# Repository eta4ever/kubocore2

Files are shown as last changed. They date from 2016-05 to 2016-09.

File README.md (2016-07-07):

3D-принтер Kubocore 2. Дальний родственник SmartCore. Точнее, был первый Kubocore, который форк SmartCore из алюминиевой трубы. А второй - из конструкционного профиля 2020 и на рельсах MGN12. Общего со SmartCore - кинематика CoreXY двухуровневая и подшипники 608zz в качестве роликов.

Все изображено в "Компас-3D". Актуальная сборка - assembly_v3 в корне. Parts - просто детали. Printed parts - соответственно, печатные.

В общем, кубик из 2020, уголки печатные, Т-гайки китайские, рельсы нетипично расположены, чтобы уменьшить подъем ремней - для двух уровней сильно актуально. Печатает. 

http://3dtoday.ru/tag/kubocore+2/

---

Чуток подробностей. Тезисно.

--XY--

8 подшипников 60zz в качестве роликов ремней. Насажены на обрезки валов 8 мм, проложены печатными шайбами.

П-образный профиль 12х15 мм под рельсой X. 

Ремни натягиваются ручками. Для компенсации неравномерности натяга можно дополнительно подтянуть ремни подручными средствами (ну, там, пружинкой от прищепки) на участке за печатающей головкой (там перехлест, "правый" ремень идет к левому краю и наоборот).

Хотэнд E3D (в моем случае Volcano) крепится за верхнее горлышко алюминиевым держателем 16-миллиметрового вала (SK16).

--Z--

Два вала 12 мм, соотв., 4 держателя SK12. Длинные фланцевые подшипники (LMF12LUU) прикручены к 12-миллиметровой фанере (насквозь), она - основание стола.

Ходовой винт - TR8x8 с латуниевой гайкой, муфта обычная "пружинка", в нее закинут шарик от подшипника, чтобы на наклон работала, а на сжатие - нет.

---

Держатели движков - от cnc-tehnologi.ru. Алярма, они не особо стандартные. Надо прикидывать, можно ли поставить обычные.

Остальное менее интересно. Электроника - любая подходящая. Работало оно на MKS Gen (Marlin 1.02), сейчас на MKS SBase (Smoothieware).

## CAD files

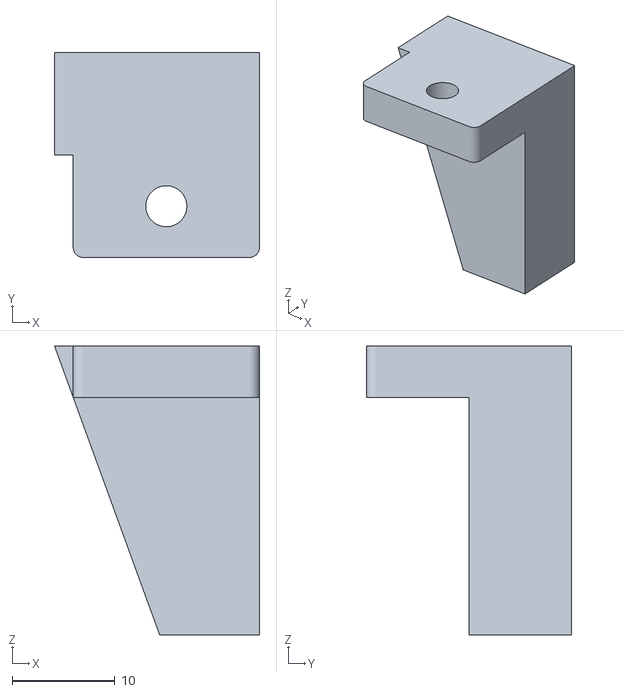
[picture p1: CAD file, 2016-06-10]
printed parts/fullgraphic-box-mountL.stl
20.0 x 20.0 x 28.2

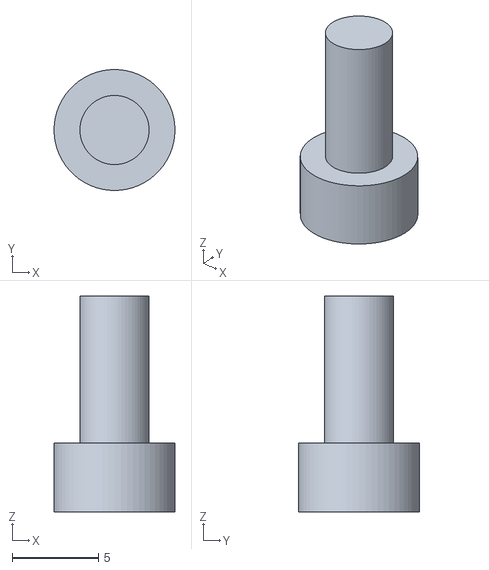
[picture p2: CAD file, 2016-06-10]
printed parts/fullgraphic-box-button.stl
7.00 x 7.00 x 12.5

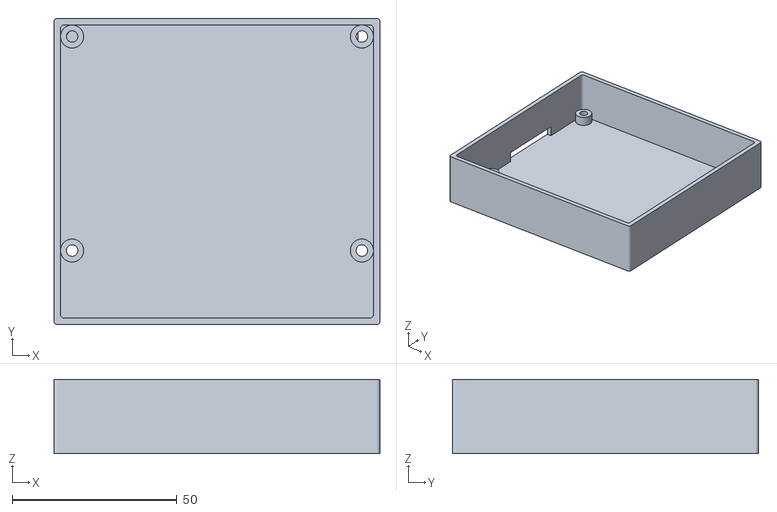
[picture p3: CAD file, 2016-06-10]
printed parts/fullgraphic-box.stl
99.0 x 93.0 x 22.5

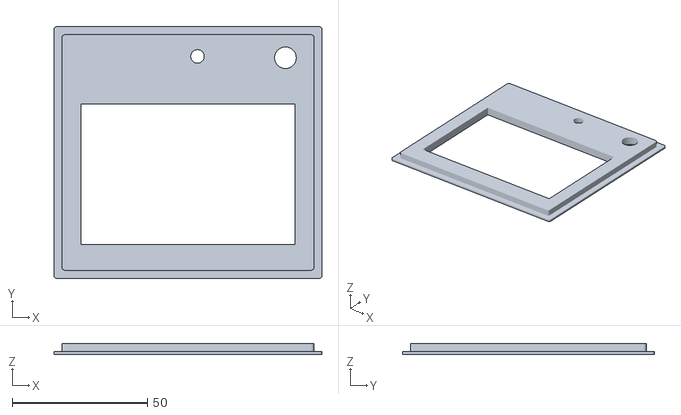
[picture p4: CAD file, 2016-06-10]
printed parts/fullgraphic-box-cover.stl
99.0 x 93.0 x 4.00

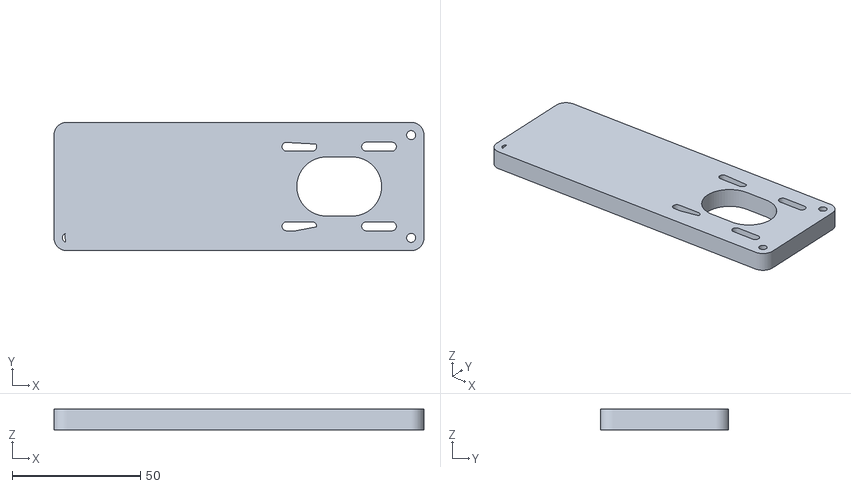
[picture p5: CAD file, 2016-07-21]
bandura extruder beta/printed/lid.stl
144.0 x 50.0 x 8.00

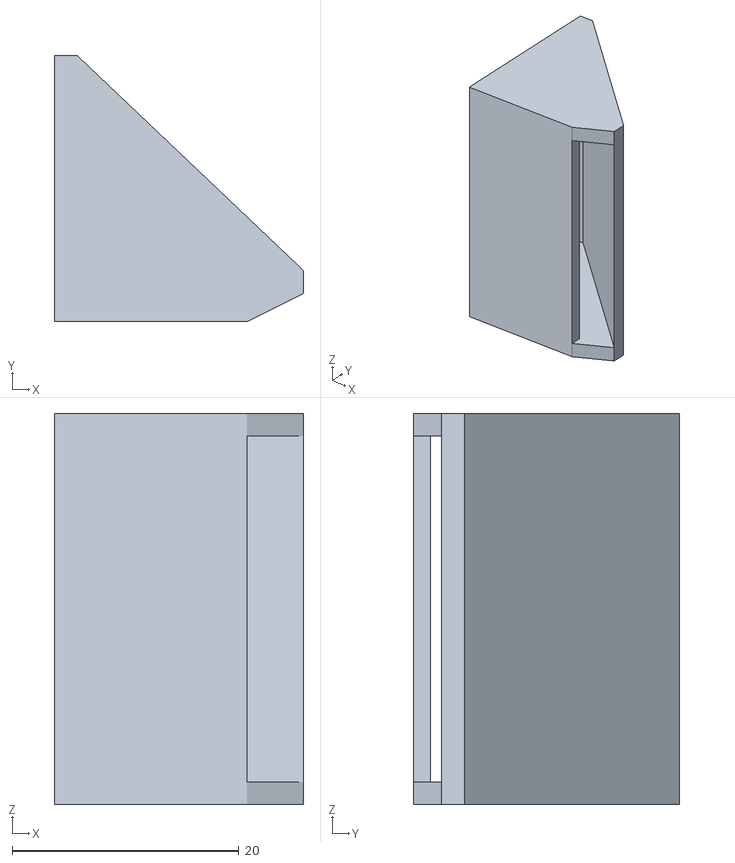
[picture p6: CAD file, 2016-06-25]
not used/printed parts/blower_nozzle_v2.stl
22.0 x 23.5 x 34.5

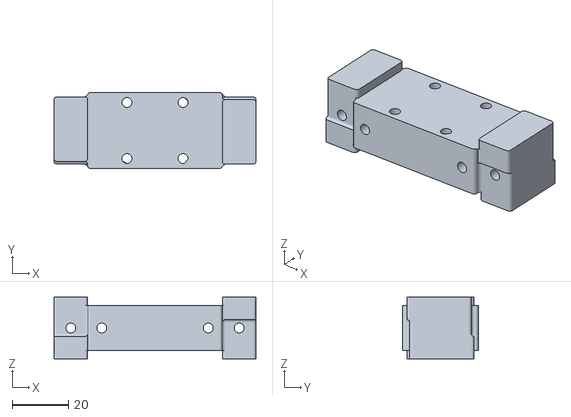
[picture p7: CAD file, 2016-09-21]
printed parts 2016-09-15/head_v3.stl
72.0 x 27.0 x 22.0

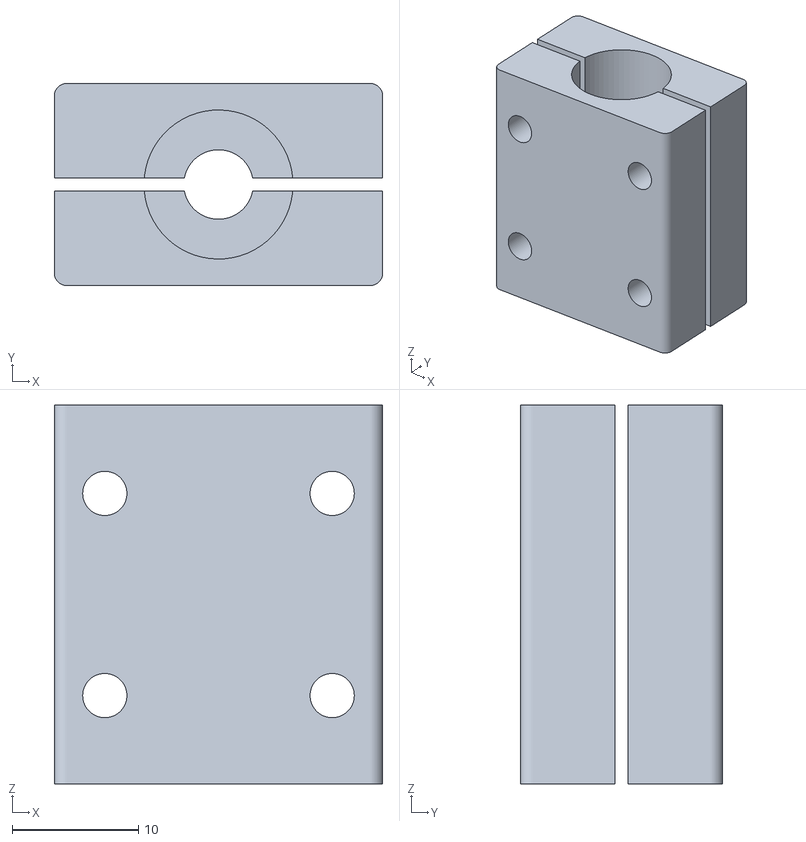
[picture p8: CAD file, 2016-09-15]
printed parts/5to11.5.stl
26.0 x 16.0 x 30.0

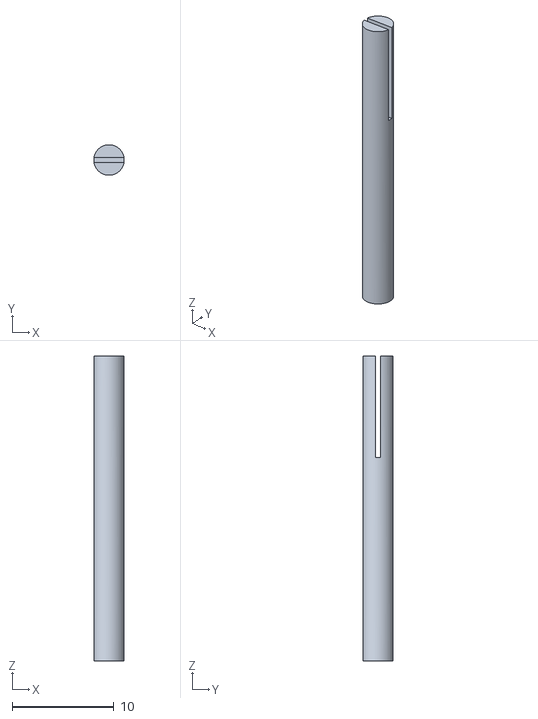
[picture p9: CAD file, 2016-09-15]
printed parts/e3dnewholder/pin.stl
3.00 x 3.00 x 30.0

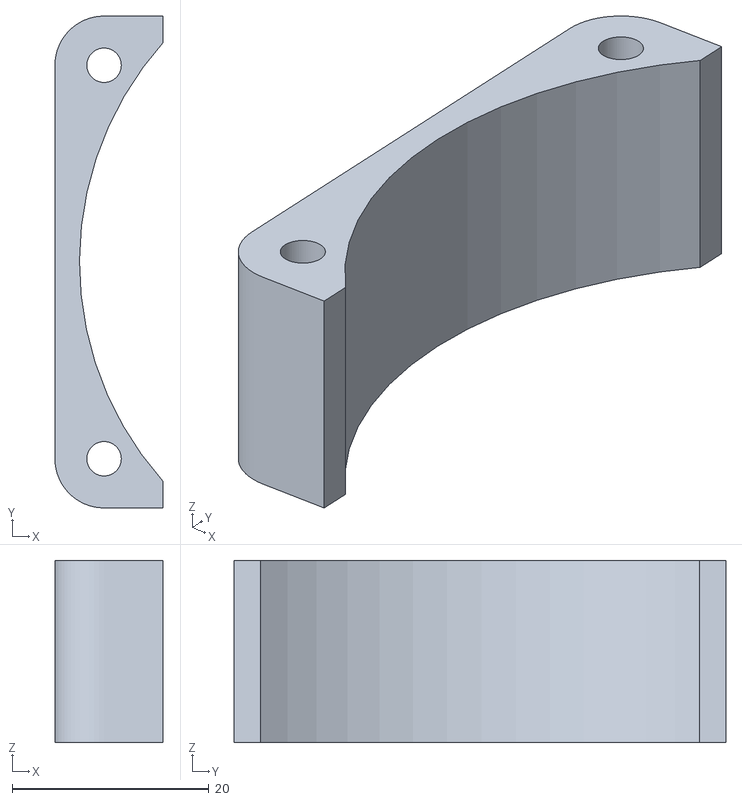
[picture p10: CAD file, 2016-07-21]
bandura extruder beta/printed/insert.stl
11.0 x 50.0 x 18.5

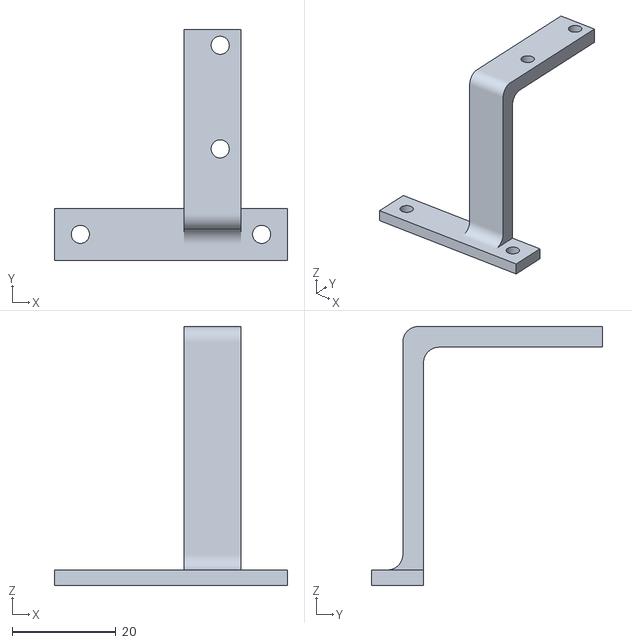
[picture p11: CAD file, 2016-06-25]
not used/printed parts/blower_holder_v3.stl
45.0 x 44.5 x 50.0

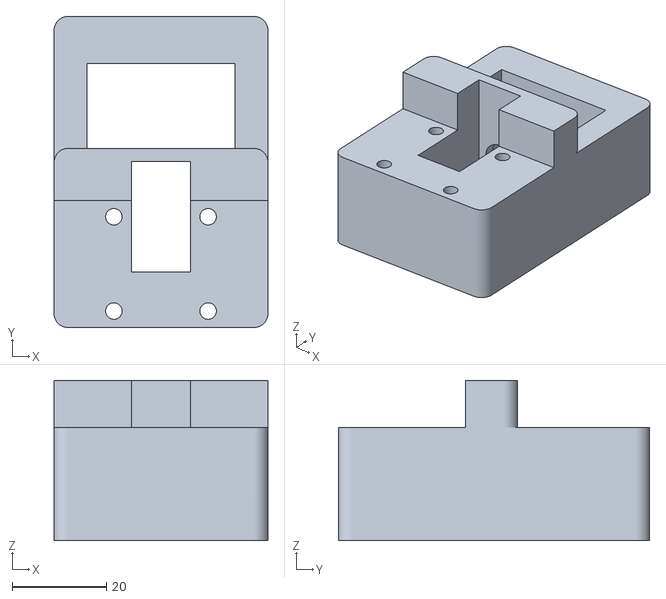
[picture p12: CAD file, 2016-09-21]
printed parts 2016-09-15/xy_v3_rep.stl
45.4 x 66.0 x 34.0

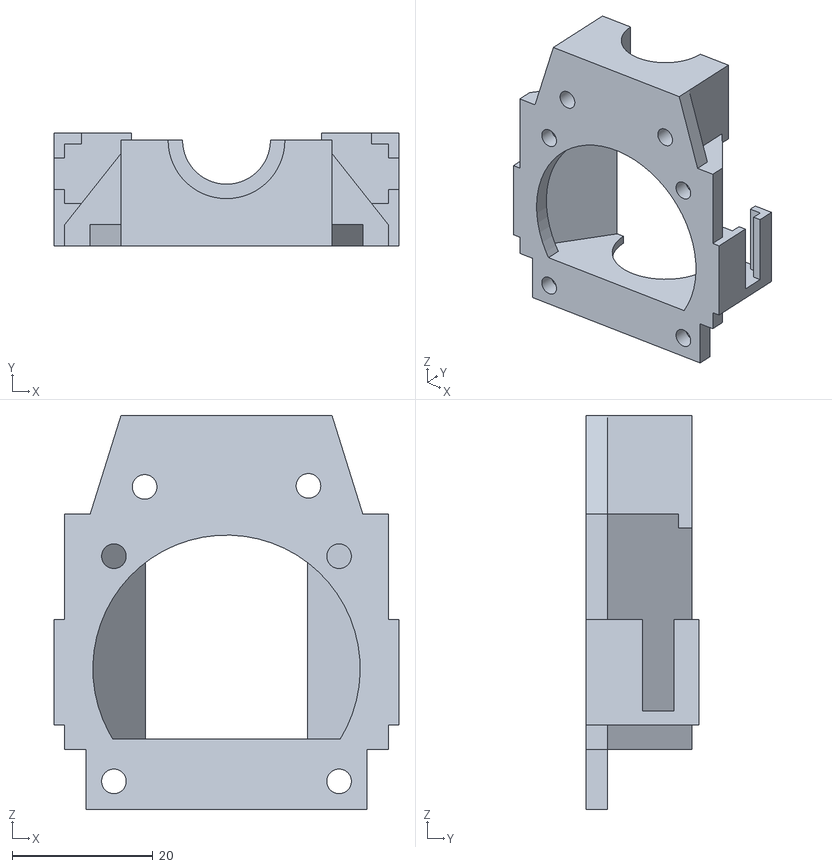
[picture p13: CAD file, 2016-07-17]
printed parts/e3dnewholder/front.stl
49.0 x 16.0 x 56.0

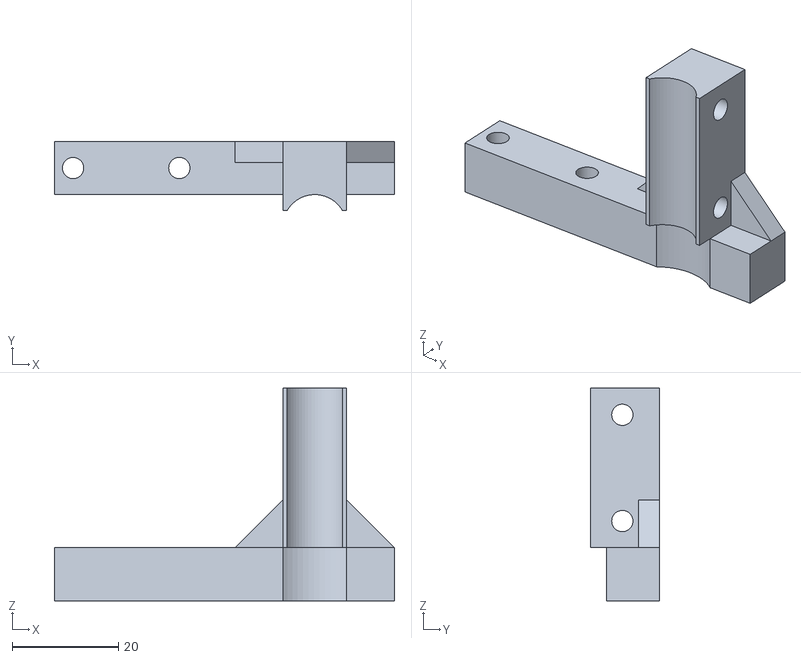
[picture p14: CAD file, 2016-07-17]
printed parts/hose_holder-head.stl
64.0 x 13.0 x 40.0

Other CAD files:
printed parts/fullgraphic-box-mountR.stl
not used/printed parts/blower_holder_v2_printable.stl
printed parts 2016-09-15/head_v3_rep.stl
printed parts/e3dnewholder/base.stl
not used/OpenSCAD parts - deprecated/head.scad
not used/OpenSCAD parts - deprecated/helper.scad
not used/OpenSCAD parts - deprecated/parts.scad
not used/OpenSCAD parts - deprecated/washer.scad
not used/OpenSCAD parts - deprecated/xy.scad
not used/OpenSCAD parts - deprecated/xyz.scad
not used/OpenSCAD parts - deprecated/z.scad
not used/printed parts/blower_holder_printable.stl
not used/printed parts/blower_nozzle.stl
not used/printed parts/z_console - 11.stl
not used/printed parts/z_console - 111.stl
not used/printed parts/z_console - 112.stl
not used/printed parts/z_console - 12.stl
not used/printed parts/z_console - 22.stl
not used/printed parts/z_console - 21.stl
not used/printed parts/z_console - 211.stl
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

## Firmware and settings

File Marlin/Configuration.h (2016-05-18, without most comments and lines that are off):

#define CONFIGURATION_H
#include "boards.h"
#define STRING_VERSION_CONFIG_H __DATE__ " " __TIME__ // build date and time
#define STRING_CONFIG_H_AUTHOR "(none, default config)" // Who made the changes.
#define SERIAL_PORT 0
#define BAUDRATE 115200
#define MOTHERBOARD 33
#define EXTRUDERS 1
#define POWER_SUPPLY 1
#define TEMP_SENSOR_0 1
#define TEMP_SENSOR_1 0
#define TEMP_SENSOR_2 0
#define TEMP_SENSOR_BED 1
#define MAX_REDUNDANT_TEMP_SENSOR_DIFF 10
#define TEMP_RESIDENCY_TIME 10  // (seconds)
#define TEMP_HYSTERESIS 3       // (degC) range of +/- temperatures considered "close" to the target one
#define TEMP_WINDOW     1       // (degC) Window around target to start the residency timer x degC early.
#define HEATER_0_MINTEMP 5
#define HEATER_1_MINTEMP 5
#define HEATER_2_MINTEMP 5
#define BED_MINTEMP 5
#define HEATER_0_MAXTEMP 275
#define HEATER_1_MAXTEMP 275
#define HEATER_2_MAXTEMP 275
#define BED_MAXTEMP 150
#define PIDTEMP
#define BANG_MAX 255 // limits current to nozzle while in bang-bang mode; 255=full current
#define PID_MAX BANG_MAX // limits current to nozzle while PID is active (see PID_FUNCTIONAL_RANGE below); 255=full current
  #define PID_FUNCTIONAL_RANGE 10 // If the temperature difference between the target temperature and the actual temperature
  #define PID_INTEGRAL_DRIVE_MAX PID_MAX  //limit for the integral term
  #define K1 0.95 //smoothing factor within the PID
  #define PID_dT ((OVERSAMPLENR * 10.0)/(F_CPU / 64.0 / 256.0)) //sampling period of the temperature routine
    #define  DEFAULT_Kp 27.86
    #define  DEFAULT_Ki 5.49
    #define  DEFAULT_Kd 35.38
#define MAX_BED_POWER 255 // limits duty cycle to bed; 255=full current
#define PREVENT_DANGEROUS_EXTRUDE
#define PREVENT_LENGTHY_EXTRUDE
#define EXTRUDE_MINTEMP 170
#define EXTRUDE_MAXLENGTH (X_MAX_LENGTH+Y_MAX_LENGTH) //prevent extrusion of very large distances.
#define COREXY
#define ENDSTOPPULLUPS // Comment this out (using // at the start of the line) to disable the endstop pullup resistors
  #define ENDSTOPPULLUP_XMAX
  #define ENDSTOPPULLUP_YMAX
  #define ENDSTOPPULLUP_ZMAX
  #define ENDSTOPPULLUP_XMIN
  #define ENDSTOPPULLUP_YMIN
  #define ENDSTOPPULLUP_ZMIN
const bool X_MIN_ENDSTOP_INVERTING = false; // set to true to invert the logic of the endstop.
const bool Y_MIN_ENDSTOP_INVERTING = false; // set to true to invert the logic of the endstop.
const bool Z_MIN_ENDSTOP_INVERTING = false; // set to true to invert the logic of the endstop.
const bool X_MAX_ENDSTOP_INVERTING = true; // set to true to invert the logic of the endstop.
const bool Y_MAX_ENDSTOP_INVERTING = true; // set to true to invert the logic of the endstop.
const bool Z_MAX_ENDSTOP_INVERTING = true; // set to true to invert the logic of the endstop.
#if defined(COREXY) && !defined(DISABLE_MAX_ENDSTOPS)
  #define DISABLE_MAX_ENDSTOPS
#endif
#define X_ENABLE_ON 0
#define Y_ENABLE_ON 0
#define Z_ENABLE_ON 0
#define E_ENABLE_ON 0 // For all extruders
#define DISABLE_X false
#define DISABLE_Y false
#define DISABLE_Z false
#define DISABLE_E false // For all extruders
#define DISABLE_INACTIVE_EXTRUDER true //disable only inactive extruders and keep active extruder enabled
#define INVERT_X_DIR true    // for Mendel set to false, for Orca set to true
#define INVERT_Y_DIR true    // for Mendel set to true, for Orca set to false
#define INVERT_Z_DIR true     // for Mendel set to false, for Orca set to true
#define INVERT_E0_DIR true   // for direct drive extruder v9 set to true, for geared extruder set to false
#define INVERT_E1_DIR false    // for direct drive extruder v9 set to true, for geared extruder set to false
#define INVERT_E2_DIR false   // for direct drive extruder v9 set to true, for geared extruder set to false
#define X_HOME_DIR -1
#define Y_HOME_DIR -1
#define Z_HOME_DIR -1
#define min_software_endstops false // If true, axis won't move to coordinates less than HOME_POS.
#define max_software_endstops false  // If true, axis won't move to coordinates greater than the defined lengths below.
#define X_MAX_POS 190
#define X_MIN_POS 0
#define Y_MAX_POS 200
#define Y_MIN_POS 0
#define Z_MAX_POS 200
#define Z_MIN_POS 0
#define X_MAX_LENGTH (X_MAX_POS - X_MIN_POS)
#define Y_MAX_LENGTH (Y_MAX_POS - Y_MIN_POS)
#define Z_MAX_LENGTH (Z_MAX_POS - Z_MIN_POS)
#define Z_PROBE_REPEATABILITY_TEST  // If not commented out, Z-Probe Repeatability test will be included if Auto Bed Leveling is Enabled.
#define MANUAL_X_HOME_POS 0
#define MANUAL_Y_HOME_POS 0
#define MANUAL_Z_HOME_POS 0
#define NUM_AXIS 4 // The axis order in all axis related arrays is X, Y, Z, E
#define HOMING_FEEDRATE {50*60, 50*60, 4*60, 0}  // set the homing speeds (mm/min)
#define DEFAULT_AXIS_STEPS_PER_UNIT   {80,80,400,100} // TR8x8
#define DEFAULT_MAX_FEEDRATE          {500, 500, 2.5, 100}
#define DEFAULT_MAX_ACCELERATION      {1000,1000,100,1000}
#define DEFAULT_ACCELERATION          2000    // X, Y, Z and E max acceleration in mm/s^2 for printing moves
#define DEFAULT_RETRACT_ACCELERATION  2000   // X, Y, Z and E max acceleration in mm/s^2 for retracts
#define DEFAULT_XYJERK                20.0    // (mm/sec)
#define DEFAULT_ZJERK                 10.0     // (mm/sec)
#define DEFAULT_EJERK                 5.0    // (mm/sec)
#define CUSTOM_M_CODES
  #define CUSTOM_M_CODE_SET_Z_PROBE_OFFSET 851
  #define Z_PROBE_OFFSET_RANGE_MIN -5
  #define Z_PROBE_OFFSET_RANGE_MAX 0
#define PLA_PREHEAT_HOTEND_TEMP 180
#define PLA_PREHEAT_HPB_TEMP 70
#define PLA_PREHEAT_FAN_SPEED 255   // Insert Value between 0 and 255
#define ABS_PREHEAT_HOTEND_TEMP 240
#define ABS_PREHEAT_HPB_TEMP 100
#define ABS_PREHEAT_FAN_SPEED 255   // Insert Value between 0 and 255
#define ENCODER_PULSES_PER_STEP 1 // Increase if you have a high resolution encoder
#define ENCODER_STEPS_PER_MENU_ITEM 4 // Set according to ENCODER_PULSES_PER_STEP or your liking
#define REPRAP_DISCOUNT_FULL_GRAPHIC_SMART_CONTROLLER
 #define DOGLCD
 #define U8GLIB_ST7920
 #define REPRAP_DISCOUNT_SMART_CONTROLLER
 #define ULTIPANEL
 #define NEWPANEL
  #define SDSUPPORT
  #define ULTRA_LCD
    #define LCD_WIDTH 20
    #define LCD_HEIGHT 5
#  define DEFAULT_LCD_CONTRAST 32
#define SOFT_PWM_SCALE 0
#define FILAMENT_SENSOR_EXTRUDER_NUM	0  //The number of the extruder that has the filament sensor (0,1,2)
#define MEASUREMENT_DELAY_CM			14  //measurement delay in cm.  This is the distance from filament sensor to middle of barrel
#define DEFAULT_NOMINAL_FILAMENT_DIA  3.0  //Enter the diameter (in mm) of the filament generally used (3.0 mm or 1.75 mm) - this is then used in the slicer software.  Used for sensor reading validation
#define MEASURED_UPPER_LIMIT          3.30  //upper limit factor used for sensor reading validation in mm
#define MEASURED_LOWER_LIMIT          1.90  //lower limit factor for sensor reading validation in mm
#define MAX_MEASUREMENT_DELAY			20  //delay buffer size in bytes (1 byte = 1cm)- limits maximum measurement delay allowable (must be larger than MEASUREMENT_DELAY_CM  and lower number saves RAM)
#define DEFAULT_MEASURED_FILAMENT_DIA  DEFAULT_NOMINAL_FILAMENT_DIA  //set measured to nominal initially
#include "Configuration_adv.h"
#include "thermistortables.h"

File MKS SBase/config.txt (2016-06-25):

# Base config

default_feed_rate	3600
default_seek_rate	3600
mm_per_arc_segment	0.5

arm_solution corexy

//alpha_steps_per_mm	80 // 1/16 GT2
//beta_steps_per_mm	80
//gamma_steps_per_mm	400 // tr8x8

alpha_steps_per_mm	160 // 1/32 GT2
beta_steps_per_mm	160
gamma_steps_per_mm	800 // tr8x8

planner_queue_size	32 // don't touch

acceleration	2000
z_acceleration	60
acceleration_ticks_per_second 1000
junction_deviation	0.02

# Stepper module configuration

microseconds_per_step_pulse	1
base_stepping_frequency	100000

# Cartesian axis speed limits
x_axis_max_speed	30000
y_axis_max_speed    30000
z_axis_max_speed    100

# Stepper module pins
alpha_step_pin	2.0
alpha_dir_pin	0.5
alpha_en_pin	0.4
alpha_current   1.0
alpha_max_rate  30000

beta_step_pin	2.1
beta_dir_pin	0.11
beta_en_pin		0.10
beta_current    1.0
beta_max_rate   30000

gamma_step_pin	2.2
gamma_dir_pin	0.20
gamma_en_pin	0.19
gamma_current	1.0
gamma_max_rate  100

# Serial communications configuration
uart0.baud_rate	115200
second_usb_serial_enable	true

# Extruder module configuration

extruder.hotend.enable	true
//extruder.hotend.steps_per_mm	100
extruder.hotend.steps_per_mm	200
extruder.hotend.default_feed_rate	600
extruder.hotend.acceleration	1000
extruder.hotend.max_speed	100

extruder.hotend.step_pin 	2.3
extruder.hotend.dir_pin 	0.22
extruder.hotend.en_pin 		0.21

delta_current	1.0

# Hotend
temperature_control.hotend.enable 	true
temperature_control.hotend.thermistor_pin    0.24
temperature_control.hotend.heater_pin        2.7
temperature_control.hotend.thermistor        RRRF100K
temperature_control.hotend.set_m_code        104
temperature_control.hotend.set_and_wait_m_code 109
temperature_control.hotend.designator        T

temperature_control.bed.enable               true
temperature_control.bed.thermistor_pin       0.23
temperature_control.bed.heater_pin           2.5
temperature_control.bed.thermistor           RRRF100K

temperature_control.bed.set_m_code           140
temperature_control.bed.set_and_wait_m_code  190
temperature_control.bed.designator           B

# Switch module for fan control
switch.fan.enable                            true             #
switch.fan.input_on_command                  M106             #
switch.fan.input_off_command                 M107             #
switch.fan.output_pin                        2.4              #
switch.fan.output_type                       pwm              # pwm output settable with S parameter in the input_on_comand
#switch.fan.max_pwm                          255              # set max pwm for the pin default is 255

# Endstops
endstops_enable                              true
corexy_homing                                true
alpha_min_endstop                            1.24^
alpha_max_endstop                            nc
alpha_homing_direction                       home_to_min
alpha_min                                    0
alpha_max                                    190
beta_min_endstop                             1.26^
beta_max_endstop                             nc
beta_homing_direction                        home_to_min
beta_min                                     0
beta_max                                     190
gamma_min_endstop                            1.28^
gamma_max_endstop                            nc
gamma_homing_direction                       home_to_min
gamma_min                                    0
gamma_max                                    190

alpha_fast_homing_rate_mm_s                  50               # feedrates in mm/second
beta_fast_homing_rate_mm_s                   50               # "
gamma_fast_homing_rate_mm_s                  4                # "
alpha_slow_homing_rate_mm_s                  25               # "
beta_slow_homing_rate_mm_s                   25               # "
gamma_slow_homing_rate_mm_s                  2                # "

alpha_homing_retract_mm                      5                # distance in mm
beta_homing_retract_mm                       5                # "
gamma_homing_retract_mm                      1                # "

#endstop_debounce_count                       100              # uncomment if you get noise on your endstops, default is 100

# Panel
panel.enable                                  true             # set to true to enable the panel code

# fullgraphic
panel.lcd                                   reprap_discount_glcd     #
panel.spi_channel                           0                 # spi channel to use  ; GLCD EXP1 Pins 3,5 (MOSI, SCLK)
panel.spi_cs_pin                            0.16              # spi chip select     ; GLCD EXP1 Pin 4
panel.encoder_a_pin                         3.25!^            # encoder pin         ; GLCD EXP2 Pin 3  
panel.encoder_b_pin                         3.26!^            # encoder pin         ; GLCD EXP2 Pin 5
panel.click_button_pin                      1.30!^            # click button        ; GLCD EXP1 Pin 2
panel.buzz_pin                              1.31              # pin for buzzer      ; GLCD EXP1 Pin 1
panel.back_button_pin                       2.11!^            # back button         ; GLCD EXP2 Pin 8
panel.external_sd                     true              # set to true if there is an extrernal sdcard on the panel
panel.external_sd.spi_channel         1                 # set spi channel the sdcard is on
panel.external_sd.spi_cs_pin          0.28              # set spi chip select for the sdcard (or any spare pin)
panel.external_sd.sdcd_pin            0.27!^            # sd detect signal (set to nc if no sdcard detect) (or any spare pin)

panel.encoder_resolution                    4	# don't know default, with no parameters skips 

panel.menu_offset                            0                 # some panels will need 1 here

panel.alpha_jog_feedrate                     6000              # x jogging feedrate in mm/min
panel.beta_jog_feedrate                      6000              # y jogging feedrate in mm/min
panel.gamma_jog_feedrate                     200               # z jogging feedrate in mm/min

panel.hotend_temperature                     200               # temp to set hotend when preheat is selected
panel.bed_temperature                        60                # temp to set bed when preheat is selected

# Example of a custom menu entry, which will show up in the Custom entry.
# NOTE _ gets converted to space in the menu and commands, | is used to separate multiple commands
custom_menu.power_on.enable                true
custom_menu.power_on.name                  Power_on
custom_menu.power_on.command               M80

custom_menu.power_off.enable               true
custom_menu.power_off.name                 Power_off
custom_menu.power_off.command              M81

# Only needed on a smoothieboard
currentcontrol_module_enable                  true


return_error_on_unhandled_gcode              false

# network settings
network.enable                               true            # enable the ethernet network services
network.webserver.enable                     true             # enable the webserver
network.telnet.enable                        true             # enable the telnet server
#network.ip_address                           auto             # use dhcp to get ip address

# uncomment the 3 below to manually setup ip address
network.ip_address                           192.168.0.189    # the IP address
network.ip_mask                              255.255.255.0    # the ip mask
network.ip_gateway                           192.168.0.105      # the gateway address
#network.mac_override                         xx.xx.xx.xx.xx.xx  # override the mac address, only do this if you have a conflict

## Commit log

2016-04-12 washer corner
    [corner.stl]
2016-04-13 учусь делать сборки
2016-04-13 учусь делать сборку
2016-04-15 сборка
2016-04-17 openscad старые запчасти на всякий
    [head.scad, helper.scad, parts.scad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]
2016-04-17 переименовал ass в assembly а то как-то обидно
2016-04-18 работа над сборкой, стол
    [parts.scad]
2016-04-18 сборка стол
    [z_console - 11.stl, z_console - 111.stl, z_console - 112.stl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]
2016-04-19 гайка шкивы
2016-04-24 сборка, размеры стола
2016-04-24 косячок с правым кронштейном
2016-04-24 z endstop
    [z_endstop1.stl]
2016-04-24 стол
2016-04-25 пара картинок
2016-04-28 sbase config.txt
    [config.txt]
2016-05-03 небольшое наведения порядка
    [head.scad, helper.scad, parts.scad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]
2016-05-03 немного прибираюсь, прерыватель концевика Z
    [xy_endstop_plate.stl, z_endstop_plate.stl]
2016-05-03 башку пофиксил, сборку наружу вытащил
2016-05-05 40mm fan
2016-05-05 обдув радиатора хотэнда
    [e3dv6_40mm.stl]
2016-05-05 бловер начал делать
2016-05-06 40-миллиметровая улитка
2016-05-07 держатель обдува детали
2016-05-07 сопло обдува детали
    [blower_holder.stl, blower_nozzle.stl]
2016-05-10 держатели гофры
    [hose_holder-head.stl]
2016-05-10 переделан крепеж улитки
    [blower_holder.stl]
2016-05-10 переделка держателя улитки
    [blower_holder(Cut 1).stl, blower_holder(Cut 2).stl, blower_holder.stl]
2016-05-11 печатная версия держателя улитки
    [blower_holder(Cut 1).stl, blower_holder(Cut 2).stl, blower_holder_printable.stl]
2016-05-15 крышка подвала
2016-06-06 MKS Gen и простенький держатель
    [mks_gen_holder1.stl]
2016-06-07 держатель кабеля
    [cable_holder.stl]
2016-06-07 стенки
2016-06-10 фулграфик и коробка к нему
    [fullgraphic-box-button.stl, fullgraphic-box-cover.stl, fullgraphic-box-mountL.stl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]
2016-06-12 переделка под узкий профиль (П 15х12) каретки X
    [xy_v2.stl]
2016-06-12 переделанный держатель бловера
    [blower_holder_v2_printable.stl]
2016-06-19 начал рисовать редуктор экструдера
2016-06-19 в топку пока редуктор
2016-06-20 смузи 1/32
    [config.txt]
2016-06-25 опять переделка держателя улитки
2016-06-25 третья версия крепления обдува
    [blower_holder_v3.stl]
2016-06-25 сопло улитки
    [blower_nozzle_v2.stl]
2016-07-04 крепление sbase
    [mks_sbase_holder.stl]
2016-07-07 эскизы стенок с размерами
2016-07-07 readme дополнил
2016-07-14 опять переделываю башку
2016-07-14 переделываю бошку
2016-07-14 переделка башки
2016-07-15 переделанная башка
2016-07-16 убрано лишнее (в not used), запилена новая башка
    [base.stl, blower_holder_printable.stl, blower_holder_v2_printable.stl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]
2016-07-17 переделан эректор на голове, пофиксена мелкая ошибка в прижиме
    [front.stl, hose_holder-head.stl]
2016-07-17 тестовая торчалка
    [pin.stl]
2016-07-19 все-таки редуктор
2016-07-19 редуктор
2016-07-20 вписал темпы в игнор
2016-07-21 stl редуктора
    [insert.stl, lid - (repaired).stl, lid.stl]
2016-08-11 экструдер
    [insert.stl, lid - (repaired).stl, lid.stl]
2016-08-15 stl большого шкива
    [lid - (repaired).stl, lid.stl]
2016-09-15 эксперимент с деталями с компенсацией наклона
    [back_holder.stl]
2016-09-20 xy с компенсатором наклона оси роликов
    [xy_v3.stl]
2016-09-20 новая башка, ин прогрысс
2016-09-21 задний правый stl
    [back_holderR.stl]
2016-09-21 упрощенная башка
    [head_v3.stl, head_v3_rep.stl, xy_v3_rep.stl]
